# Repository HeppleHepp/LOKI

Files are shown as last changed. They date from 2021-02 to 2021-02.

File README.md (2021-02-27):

# README

## LOKI

Developement of telemetry and data collection using a microcontroller \(Arduino, ESP32 etc\) to output a PWM signal to a speed controller such as the 4QD porter 5/10.

In this repository you will find incremental developement to find the best solution to operating and using 24V DC batteries and motor as found on the Greenpower \(www.greenpower.co.uk\) regulations page. Electronics \(Loki Board\) and the software is free of licence, however, the board will be made available to purchase directly from me as a private agreement. \(email: coalescence.gp@gmail.com\), but feel free to try and have a good hack at it ;\).

## History:

Back in 2019 I had started my A-level in Design Technology and wanted to create a product that would allow better team communication, this eventually transpired to making a battery status monitor that beamed an 433MHz signal to the pitlane during the races. The voltage was found using a potential divider on a raspberry Pi and the string was encoded into a Hex signal which then used precise timers to create the packets needed to allow AM carrier transmition.

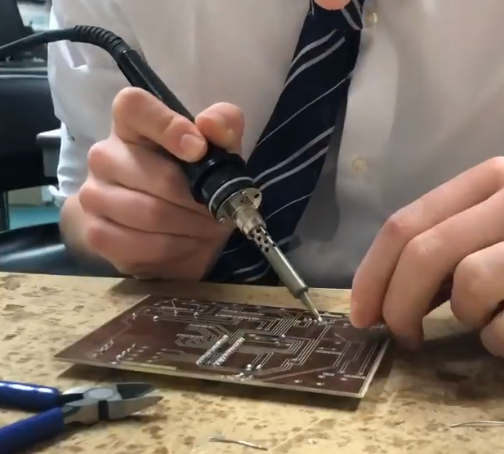
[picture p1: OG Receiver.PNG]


This was a massive headache, clunky and inefficient \(But I got the A\* i needed hehe\).

In March 2020, during the covid-19 pandemic, I suddenly found that I had plenty of time to think of a better solution, which was when I started to research about hobbiest electronics and microcontrollers such as the arduino. They offered a more efficient/code logic rather than using logic gates to encode data. Also, having a microcontroller allowed for more data to be gathered, which was the moment I realised much, much more could be achieved. Since then I have been developing sensor data based circuits that can monitor a greenpower cars 'vital systems'. In July 2020 I was no longer a member of BGS Greenpower \(Bristol Grammar School\) and I joined a close friend's team called Coalescence GP which included his first car Icarus. With a new team and direction I set about making the next car monitoring system.

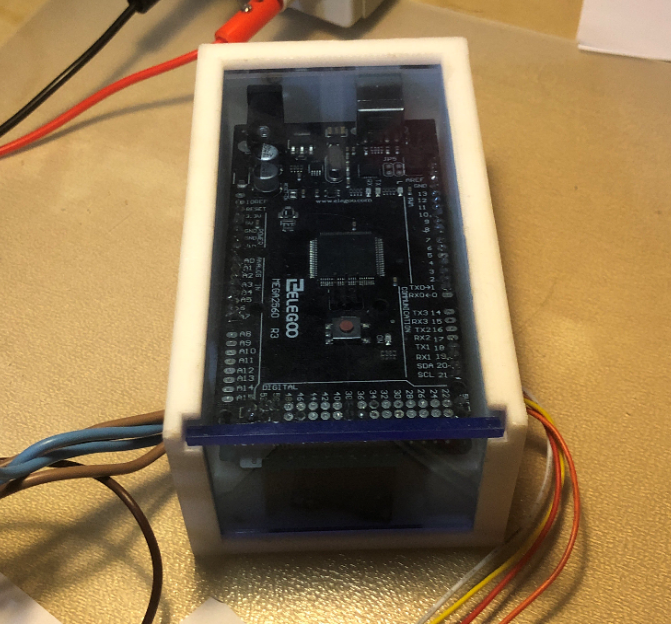
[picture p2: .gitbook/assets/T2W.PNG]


The first version of this was called T2W \(The Thrust Weapon, don't ask why\) and while it was rigged with glitches and poor design ethos it did the job and in september of 2020 gave us some valuable current vs time data, saved to an SD card, which is arguably the most important data you can collect. There was capability to gather voltage, Temperature, and RPM, but a lack of a solid testing environment due to COVID meant it was the first time the board was being used in that environment. But still I was determined to get a better understanding of the potential microcontrollers offered.

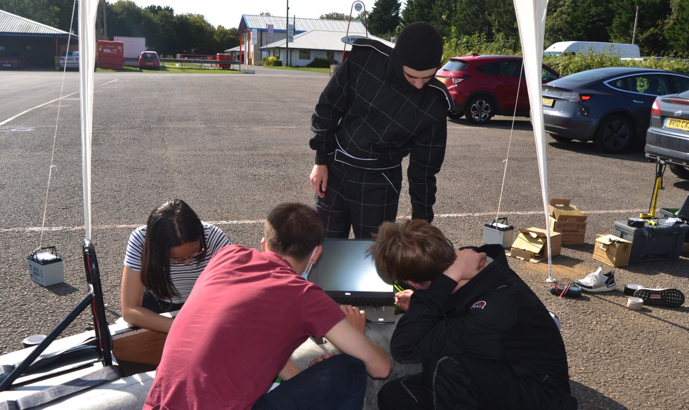
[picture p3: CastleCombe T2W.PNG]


Loki is my latest developent of this journey, and is the design I hope to iterate on over at least the next 2 years. I will be developing it in parallel with my course at university and will deploy updates and provide active support to anyone who wishes to use the board.

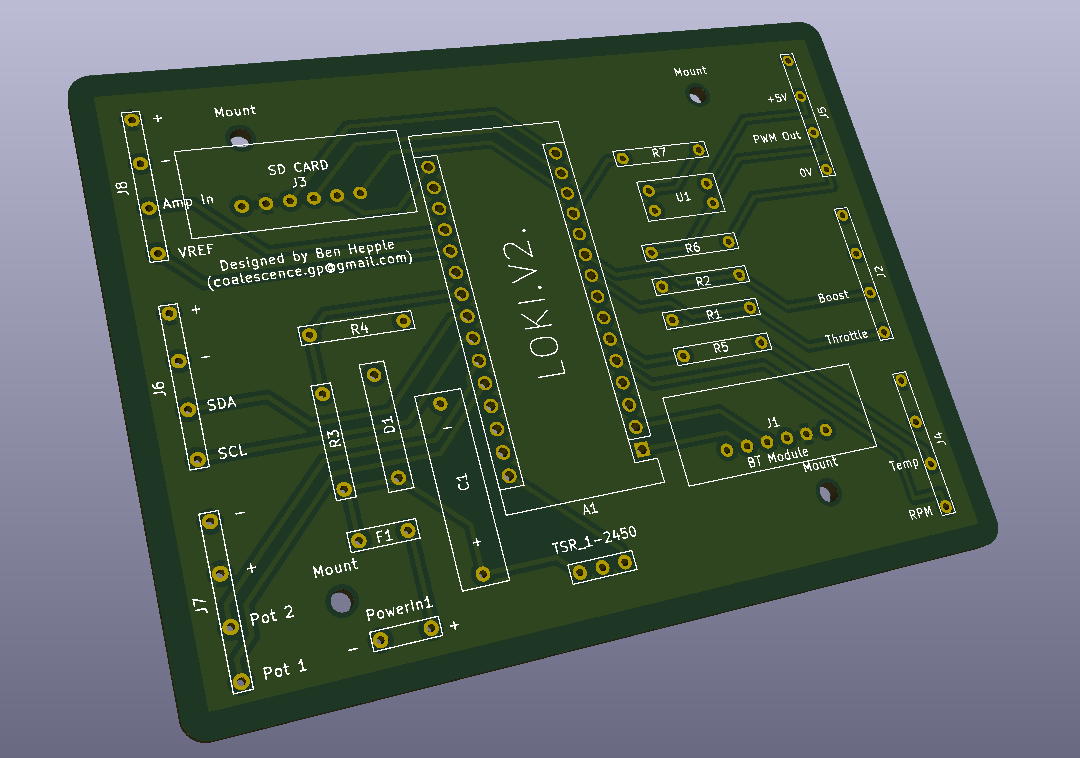
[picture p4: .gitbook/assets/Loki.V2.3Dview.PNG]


## Board features:

Firstly, it cannot be ignored that anyone who has previously looked at different option for adding data telemetry and monitoring of systems has more than likely come across the WeChook racing fellas who developed a very realiable system called the Echook Nano which is arguably the most widely used kit that fulfills this purpose. It offers pretty much the exact same features as LOKI, but having been in development for many years now it does offer a more tried and relaible system. The Echook Nano documentaion \([https://docs.echook.uk/](https://docs.echook.uk/)\), has offered me with plenty of wisdom and I have also spoken to the very active developers to confer with them over design choices for LOKI, so they only have my graditude and I have no intention of competing with them \(don't think I could even if I tried to be honest\). However, didn't stop me from trying to make my own custom board that fulfills my own specification and allows me to tailor it to my needs. All in all, thanks Rowan :D

**Features included:**

**Current sensing** up to 150 amps with a resolution of 0.25A \(Could be improved with an Op Amp :/ \)

**Battery voltage** reading \(Max 30V as there is a 1/6 ratio to step down to the 5V arduino Pin \)

**Motor RPM** \(This is done using an infrared variable distance circuit that triggers an external interrupt on the board\)

**Motor Temperature** \(This only samples the temperature with a very high accuracy every 6 seconds because does take considerable processing power\)

**Race Time** \(Only records the time since the board was switched on. So if the +24V into the board is turned off when the car is turened of the clock will reset\)

**Data Logging** \( saves all the above data into a text document, with each variable seperated by a comma which excel loves :\) \)

**Bluetooth Extension** \(A bit of a last ditch addition, there is no functionality in the software to use this currently, but it's there incase you wish to develope that yourself\)

**2 Button inputs** \(Named on the board as Throttle and Boost, This can be configured as other functions if you are using a Variable throttle\)

**2 Variable throttle or ADC ports** \(These are left spare so addition sensors or a twist grip throttle can be added onto the board where required \(some exceptions will apply\)\).

**For more information please open the PDF in the Main commit**

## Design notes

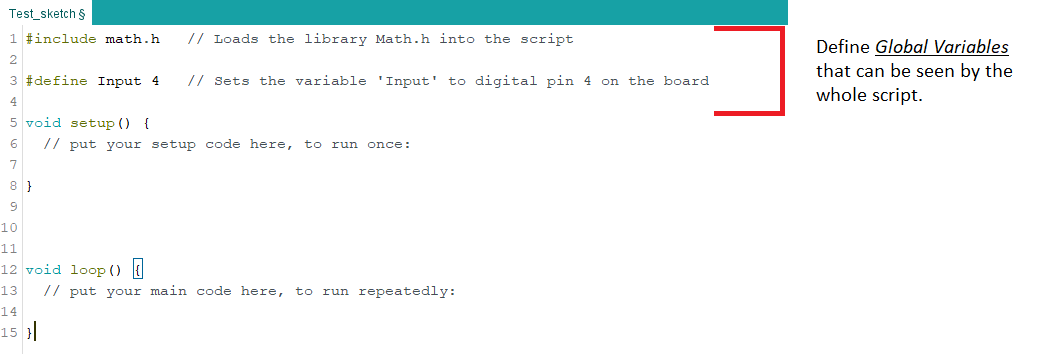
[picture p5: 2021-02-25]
.gitbook/assets/initialisation-desc.png

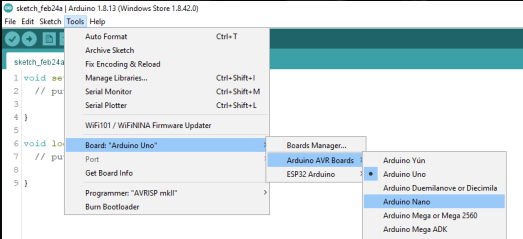
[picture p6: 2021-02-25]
.gitbook/assets/board-selection.png

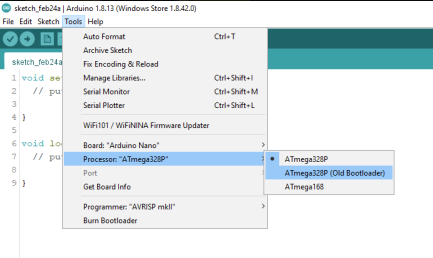
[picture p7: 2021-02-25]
.gitbook/assets/processor-selection.png

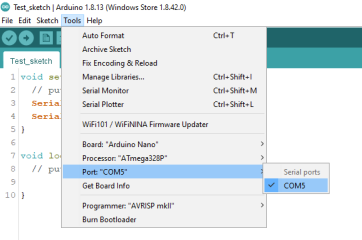
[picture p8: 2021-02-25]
.gitbook/assets/port-selection.png

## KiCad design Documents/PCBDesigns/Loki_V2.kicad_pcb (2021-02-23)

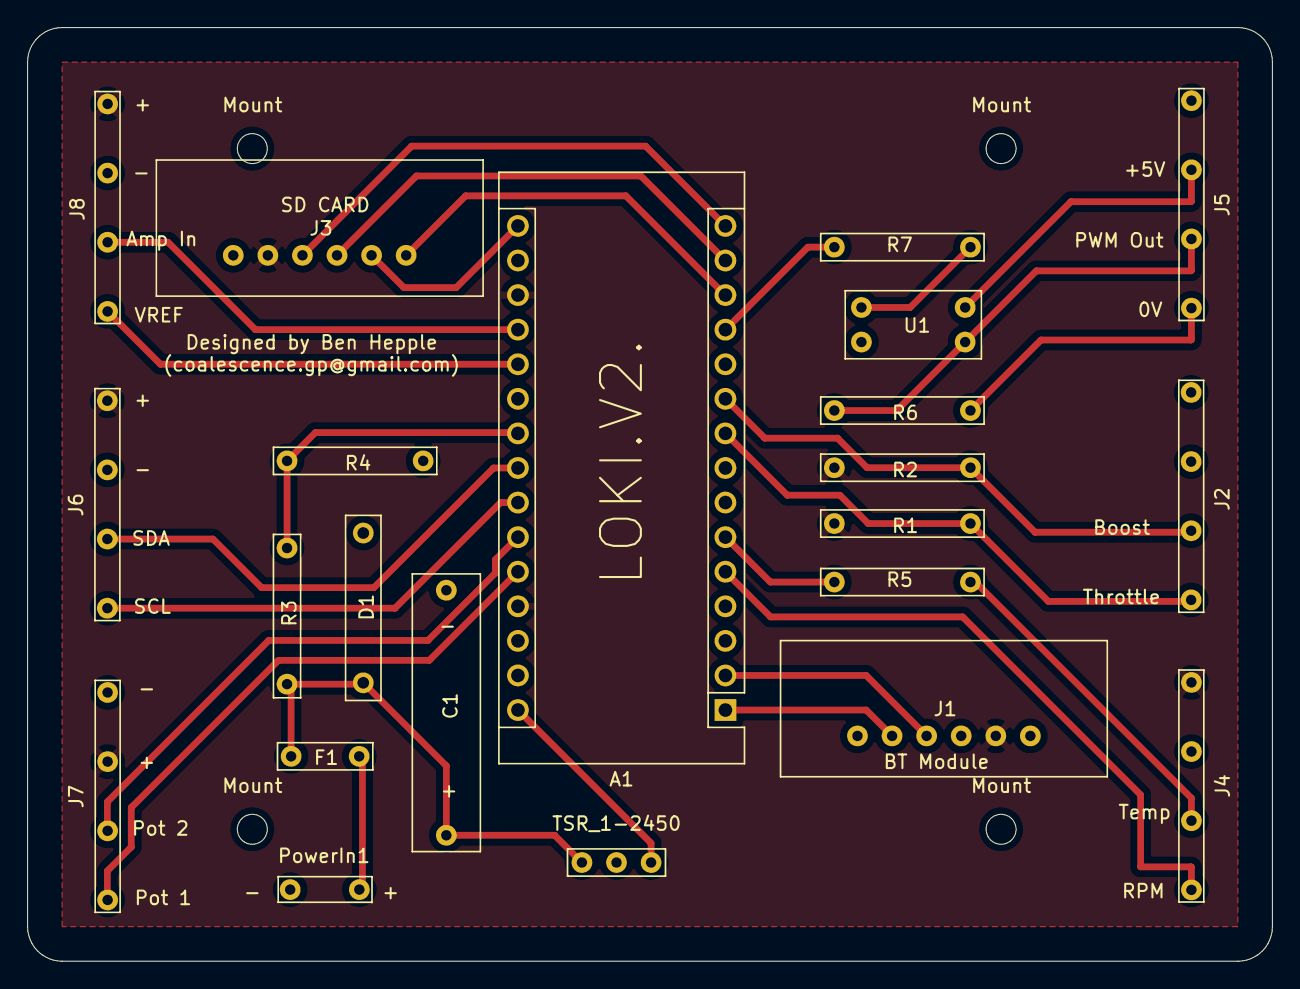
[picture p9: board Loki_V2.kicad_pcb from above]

Board: 2 copper layers, 91.4 x 68.6 mm, 26 parts (0 on the bottom side), 28 nets.

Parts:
A1: Arduino_Nano_v3.x; Arduino_Nano
C1: 22uF 63V; 22uF_Axial_Capacitor
D1: 1N5819RLG; Schottky
F1: 0.5A P-Fuse; PolyFuse
J1: Bluetooth_Ext; SD_Card
J2: Bool_Input; Screw_Terminal_X4
J3: SD Card Port; SD_Card
J4: RPM&Temp; Screw_Terminal_X4
J5: PWM Out; Screw_Terminal_X4
J6: LCD Display; Screw_Terminal_X4
J7: Dual Pot; Screw_Terminal_X4
J8: Current Sensor; Screw_Terminal_X4
Mount: MountingHole_2.2mm_M2
Mount#2, Mount#3, Mount#4: MountingHole_2.2mm_M2
PowerIn1: Input; Screw_Terminal_X2
R1, R2: 10K; Default_Resistor
R3: 82K; Default_Resistor
R4: 16K; Default_Resistor
R5: 5.1K; Default_Resistor
R6, R7: R; Default_Resistor
TSR_1-2450: Screw_Terminal_01x03; 2.54mmX3
U1: SFH617A-1; Optocoupler_K1010_B

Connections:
0V: A1.4, C1.2, D1.2, J1.4, J2.1, J2.2, J3.1, J4.3, J6.1, J7.2, J8.3, PowerIn1.2, R4.2, TSR_1-2450.2, U1.2
+5V: A1.18, A1.27, J1.5, J3.2, J4.4, J6.2, J7.1, J8.4, R1.1, R2.1
+24V: C1.1, D1.1, F1.1, R3.1, TSR_1-2450.3
Amp_In: A1.19, J8.1
BT_Input: A1.2, J1.3
BT_Output: A1.1, J1.2
Bat_Read: A1.22, R3.2, R4.1
Boost: A1.10, J2.3, R2.2
ChipSelect: A1.13, J3.6
MISO: A1.15, J3.3
MOSI: A1.14, J3.4
unnamed: F1.2, PowerIn1.1
unnamed: J4.1, R5.1
unnamed: J5.1, U1.4
unnamed: J5.3, R6.1, U1.3
unnamed: J5.4, R6.2
unnamed: R7.1, U1.1
PWM: A1.12, R7.2
Pot_1: A1.25, J7.3
Pot_2: A1.26, J7.4
RPM_Int: A1.5, J4.2
SCK: A1.16, J3.5
SCL: A1.24, J6.4
SDA: A1.23, J6.3
Temp: A1.6, R5.2
Throttle: A1.9, J2.4, R1.2
VREF: A1.20, J8.2
Vin: A1.30, TSR_1-2450.1

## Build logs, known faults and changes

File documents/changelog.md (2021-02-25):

# CHANGELOG

This page lists/highlights any changes or uplaods to this documents folder.

**23/02/2021** Uploaded loki V.2 schematic, PCB design.

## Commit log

2021-02-23 KiCad file upload
    [Loki_V2.sch]
2021-02-23 Add PCB file
    [Loki_V2.kicad_pcb]
